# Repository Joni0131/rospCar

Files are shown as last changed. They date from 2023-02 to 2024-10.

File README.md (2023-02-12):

- [rospCar](#rospcar)
- [Work progression](#work-progression)
  - [1. Old System](#1-old-system)
  - [2. Planning](#2-planning)
  - [3. ESP-32](#3-esp-32)
  - [4. Brain](#4-brain)
- [Resume](#resume)

# rospCar

This repository contains the whole redevelopment of an old RC car.
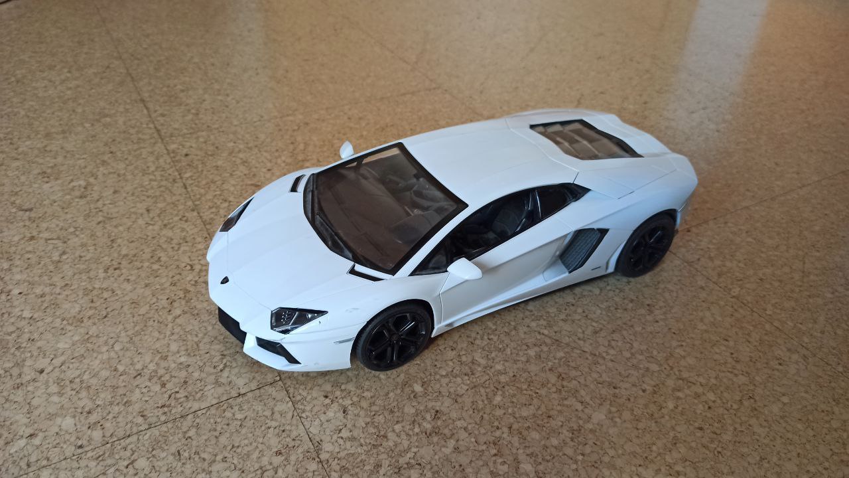
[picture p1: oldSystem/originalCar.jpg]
Old Car

To change the control system to an esp32 and a ROS communication with the computer to potentially implement a SLAM algorithm.

# Work progression

I structured my work in the following four steps. Those are shortly discussed on this page for more detailed information on each step please correspond to each designated page.

## 1. [Old System](oldSystem/)

The first step of the redevelopment process consists of understanding and checking the currently used electronics. As well as their functionality.

## 2. [Planning](upgradePlan/)

In the second phase, I chose the requirements for the new car, ordered parts that fulfill those requirements as well as designed the new circuit diagram.

## 3. [ESP-32](esp/)

The third step is considered the heart of the hardware development process. Here I define the functional requirements for the esp-32 and implement those decently.

## 4. [Brain](brain/)

Last but not least I design the other side of the communication and control algorithm for this project on the computer. The computer software is calculating the movements of the car and is using the sensor data to do this. Furthermore, it will be using a SLAM algorithm to map the whole area and it will be possible to go to certain locations easily.

# Resume

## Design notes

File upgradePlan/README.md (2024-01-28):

- [2. Planning](#2-planning)
  - [2.1 Funktional requiremnets](#21-funktional-requiremnets)
  - [2.2 Reqiered Hardware](#22-reqiered-hardware)
  - [2.3 Circuit Diagram](#23-circuit-diagram)

# 2. Planning
In this folder, I am planning the improvements for the rospCar inclusive of the new circuit diagram.

## 2.1 Funktional requiremnets

The rospCar has to fulfill multiple requirements.
 - steering
 - impulsion
 - controlling
 - voltage regulation
 - communication with another device via WIFI
 - environment tracking
 - front and back lights
 - similar appearance to the old system
 - speed information
## 2.2 Required Hardware
To fulfill those requirements multiple hardware components are necessary.
- For steering, use a [SG90 Micro Servomotor](http://www.ee.ic.ac.uk/pcheung/teaching/DE1_EE/stores/sg90_datasheet.pdf). With such a motor the steering accuracy can be improved.
- The impulsion motor is defective so a new motor has to be inserted. For this, I bought a new [motor](https://www.luedeke-elektronic.de/DC-Kleinmotor-2-5V-6V-DC-210mA-14-500U-Min-MOT2.html) of a similar size.
- As a motor controllers, I am using two L9110H.
- To regulate the voltage going to the motor I am using the voltage regulator LM317T.
- Because the car should be able to communicate with another device using WIFI, I need a WIFI module. However, I want to use ROS2 as the communication system between those devices. This is a problem because on most really small microcontrollers it is not supported. I choose [micro-ROS](https://micro.ros.org/) which is capable of running on such small chips. But support for microcontrollers to communicate with WIFI is limited so I choose the [ESP-32](https://www.espressif.com/en/products/socs/esp32) as my main microcontroller.
- For environmental tracking there are multiple options:
  - <ins>Ultrasonic sensor:</ins> This is a cheap method to detect objects and their distance. However, I am not sure how accurate this tracking is gonna be and so it is a bad option for a SLAM algorithm. But I still wanna try it I bought the HC-SR04 as an ultrasonic sensor.
  - <ins>ToF sensor:</ins> Because ToF sensors can detect distances quite accurately it is a good option for a SLAM algorithm. However, it has to be kept in mind that transparent objects could not be detected. Another disadvantage of those sensors is that it only detects objects at the same height as the sensor. Even though I decided I want to use such a sensor. So I bought the VL53L0/1XV2 and will try to use those.
  - <ins>Camera:</ins> A camera would be good to get colors of the surroundings as well as a huge part of it. Because of the lens. I am currently not sure if I will be using a camera however if I want to add one I will be adding the 0V2640 camera to the ESP-32.
- The lights of the old system can still be used.
- The speed of the rospCar is detected with an accelerometer ITG/MPU6050/GY-521.
- For the electric circuit, I need a few resistors, capacitors and wires.
## 2.3 Circuit Diagram
### 2.3.1 V0.1
To test that the baisic functionality of driving and steering is working my circuit design does not include any environment sensors only the acceleration sensor, the motors and the LED's.
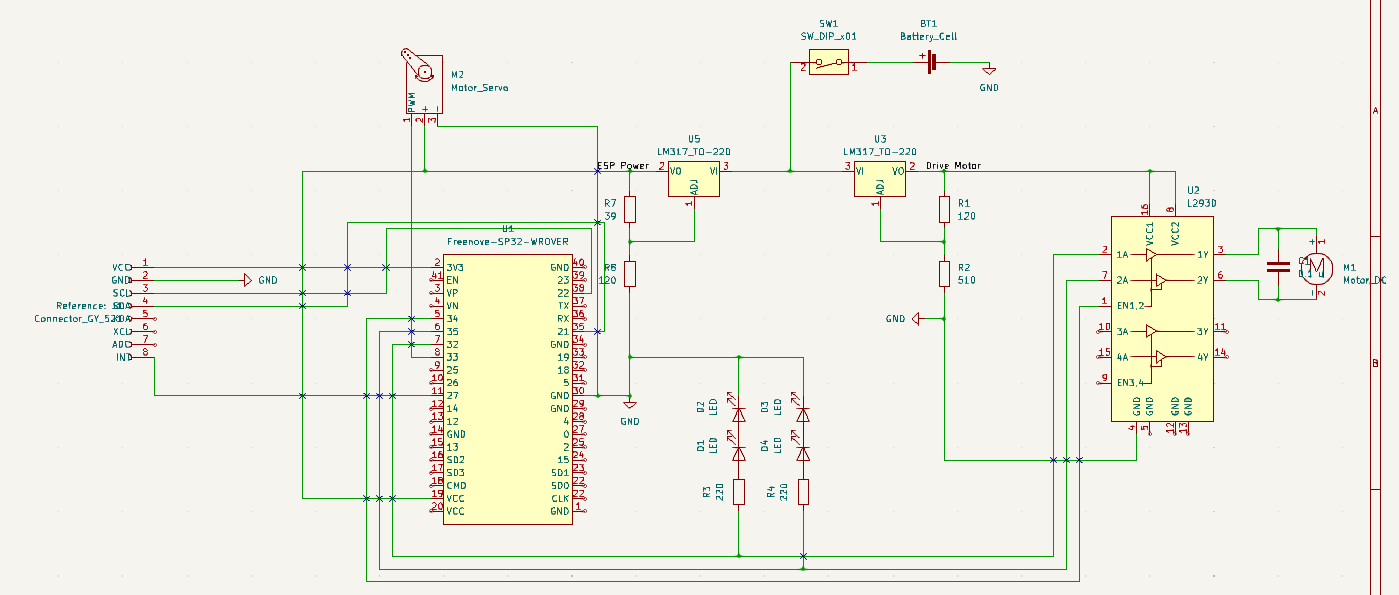
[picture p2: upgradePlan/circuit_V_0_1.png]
Circuit Diagram V0.1


#### 2.3.1.1 Learnings
When building and implementing the first functionalitis I learned that I can't use the Pin's 34-39 for output signals. Also all Pins that have the ACD2 connected can't be used because of the needed Wifi. Those the relevant pins have to be rearanged.

Also the LED's can't be connected in this way so that has to be changed as well.

For a third optimization it might be neccessary to increase the voltage for the impulsion motor drive. However, it has to be keept in mind that that voltage is also powering the L293D those it should not be overvoltaged. It can also be considered to exchange the LM317 for another trasformer that is cappable of higher current.

### 2.3.2 V0.2
To fully implement and to consider all hardware limitations I am now adding a Ultarsonic and Time-of-Flight sensor to the system including some of the learnings from before.
Circuit Diagram V0.2

#### 2.3.2.1 Learning
The motor is still not starting without help and the motor will get power in the boot process because the motor driver is enabled when it is booting.

### 2.3.3 V0.3
To get the motor starting I separated the Power circuit for the L293D and the motor power circuit. I also added a inverter based on a transistor for the enable signal for the motor driver because the esp pin will always be in the HIGH state in the boot process.
Circuit Diagram V0.3

## 2.4 PCB design

After a few schematic iterations I started designing the PCB.

### 2.4.1 V0.3
To design the PCB I added footprints to all the schematic symbols in KiCad and than placed it on a board. I then used FreeRouting to do a first automated routing for the PCB. I decided that the width of each lane is with 1 mm more than enough to handle the load of the system.

Because this is my first designed board and also the first prototype I did not optimize the length of each line and those reduced latency. In this setup it is more than enough like that and can be done in the future.

PCB Layout V0.3

Here a not complete 3D image of the planed PCB.
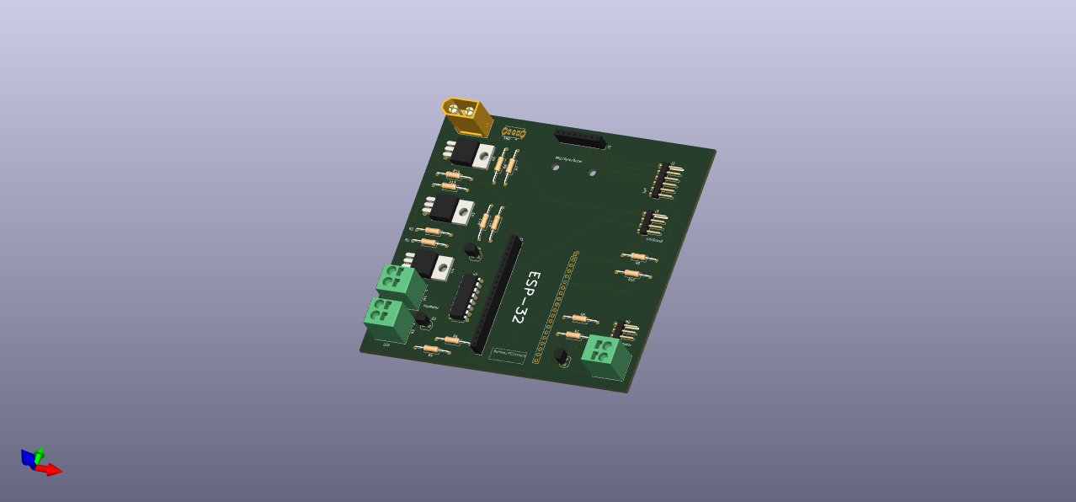
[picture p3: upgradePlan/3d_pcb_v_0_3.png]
3D PCB V0.3
 

And here the first soldered PCB.
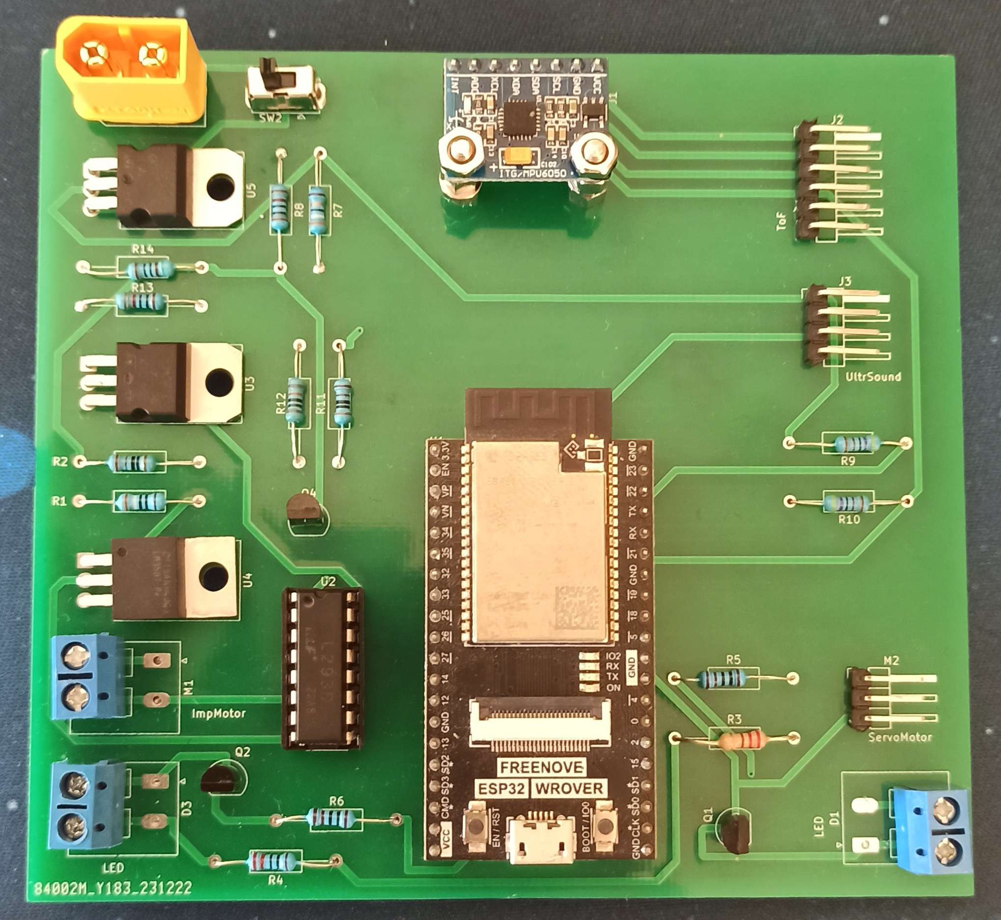
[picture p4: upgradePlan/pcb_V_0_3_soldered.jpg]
PCB V0.3 Soldered


#### 2.4.1.1 Learningdd

The pcb is still way to big. Those the next iteration needs to be smaller. Another learning is that the motor controller and the 3 voltage regulators are getting quite hot after a short test. Those I will add some kind of heat sink to them.

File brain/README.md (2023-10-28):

- [4. Brain](#4-brain)
  - [4.1 Requirements](#41-requirements)
  - [4.2 Realisation](#42-realisation)

# 4. Brain

## 4.1 Requirements

- The Brain is using ROS2 to communicate with the ESP
- The Brain sends controll instructions to the ESP
- The Brain is collecting and processing the sensor data.

Later:
- The Brain is using the sensor data to derive the controll instructions
- The Brain is using a SLAM algorithm.

## 4.2 Realisation

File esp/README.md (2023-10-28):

- [3. ESP-32](#3-esp-32)
  - [3.1 Requierements](#31-requierements)
  - [3.2 Realisation](#32-realisation)

# 3. ESP-32 

## 3.1 Requierements

- The code should be written and compiled with PlatformIO
- The ESP32 is using microROS to communicate with the Brain that is running ROS2
- The ESP has to controll the motors.
- It has to collect the sensor data and send it to the Computer.

## 3.2 Realisation

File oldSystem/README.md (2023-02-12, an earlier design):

- [1. Old System](#1-old-system)
  - [1.1 Components](#11-components)
  - [1.2 Schematic](#12-schematic)
  - [1.3 Testing](#13-testing)
    - [1.3.1 FA-130](#131-fa-130)
    - [1.3.2 260s-18130-38](#132-260s-18130-38)

# 1. Old System

I opened the car cover to reveal the internal structure of the RC car.<br>
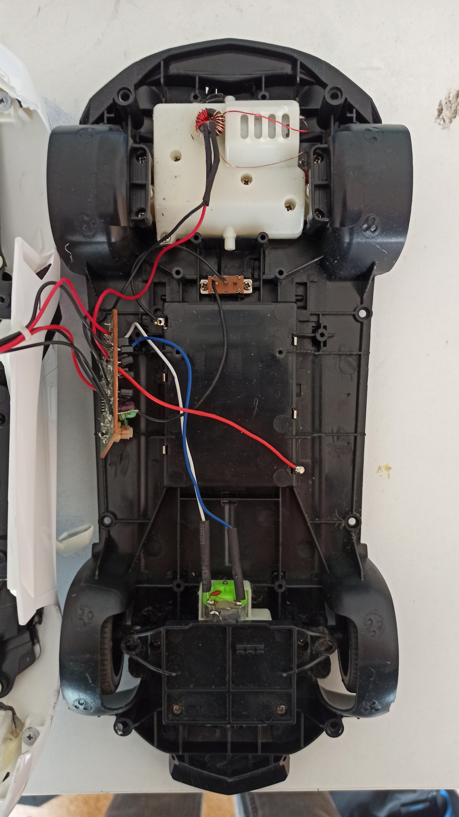
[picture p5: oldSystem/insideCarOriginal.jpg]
insideCarOriginal
<br>
As can be seen, the car's internals is pretty basic.

## 1.1 Components

- 1x FA-130 motor (steering)
- 1x 260s-18130-38 motor (impulsion)
- 1x RX-2C (controller)
- 1x PCB
- 2x C8050 (transistor)
- 2x C8550 (transistor)
- 2x D882 (transistor)
- 2x B772 (transistor)
- 4x C9014 (transistor)
- LEDs
- cable
- batterie department
- resistors 
- capacitors
- wires
- power switch

## 1.2 Schematic

To understand the control system of the RC car I partially analyzed the PCB and drama and created a [circuit diagram](initialSystem/) in kicad based on those observations.<br>
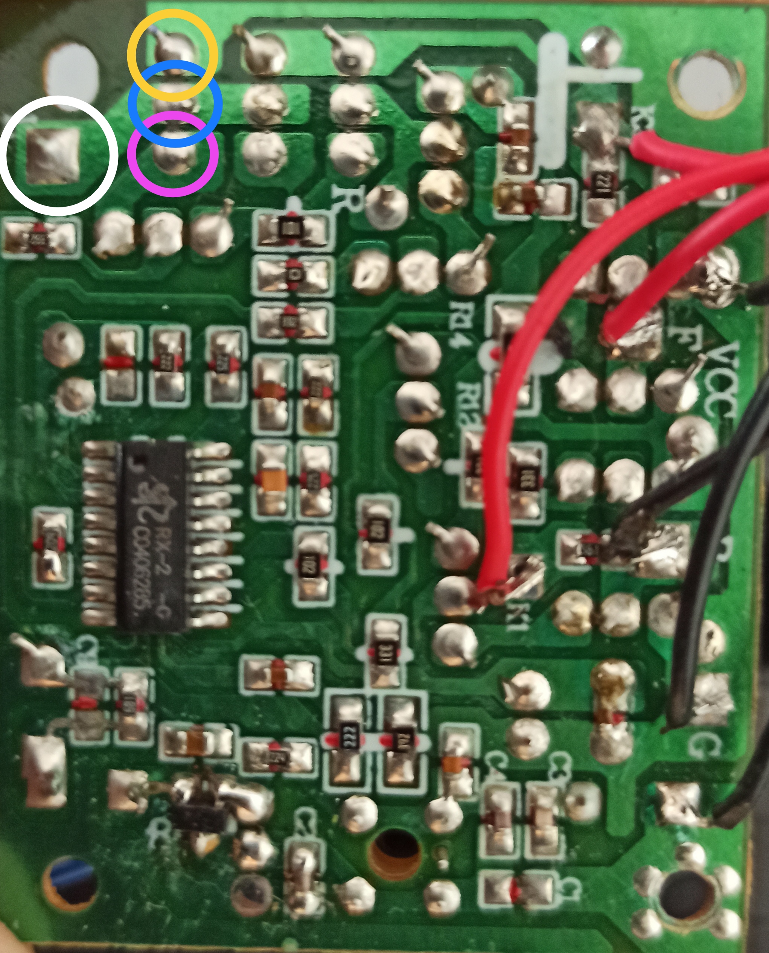
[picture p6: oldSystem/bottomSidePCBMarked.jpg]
bottomSidePCBMarked

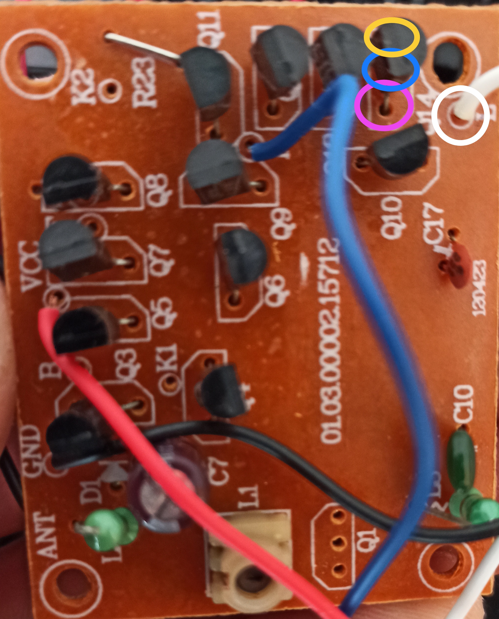
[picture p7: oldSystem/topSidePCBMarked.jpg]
topSidePCBMarked
<br>
Here is the partial circuit diagram as an image.<br>
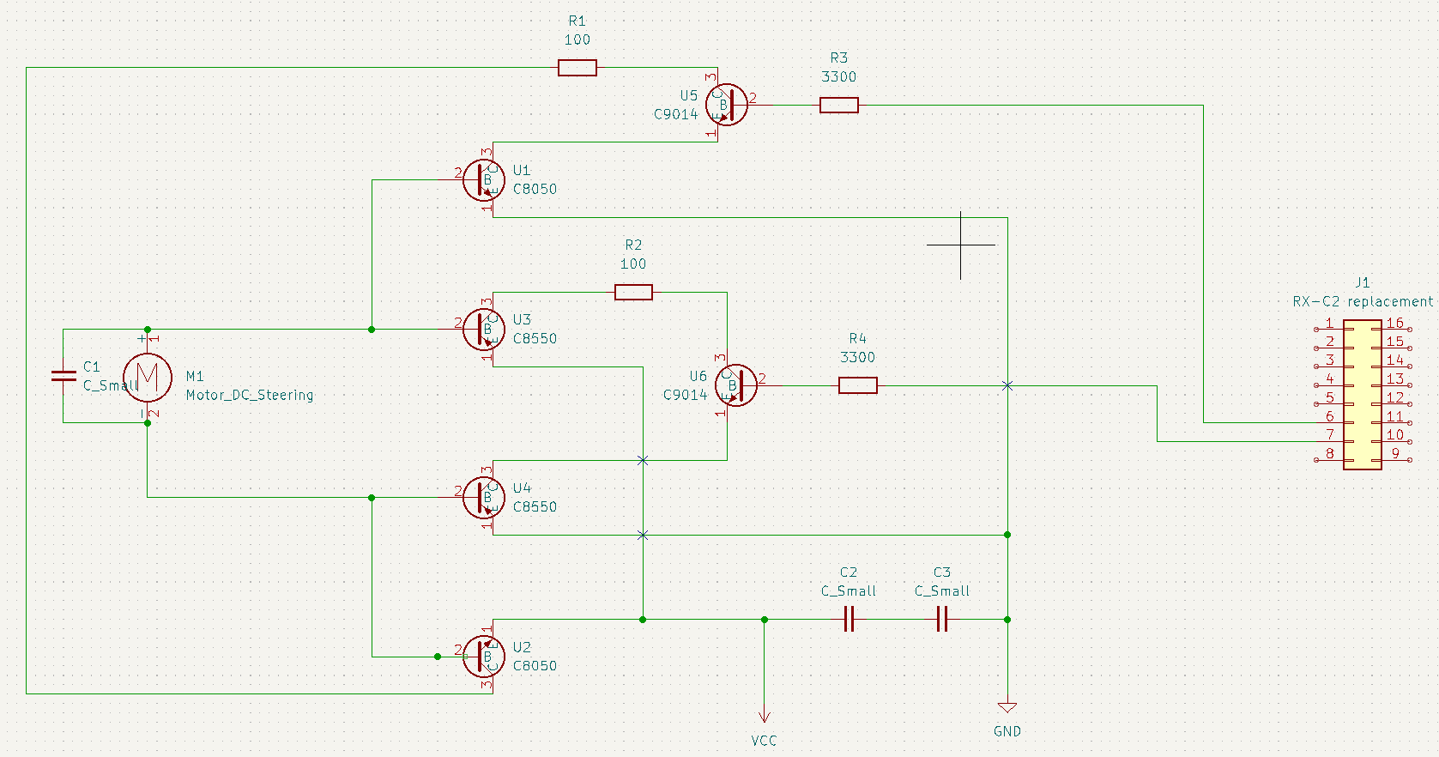
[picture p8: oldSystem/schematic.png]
schematic


However, I am a bit confused because the motor is connected to the middle part of all 4 transistors which is normally used to control the current running through the transistor. So I am not sure if I made an error creating the schematic based on the PCB or if there is some other information that I am missing.
So if anyone has an explanation for this I am more than happy to communicate with you regarding this issue.

## 1.3 Testing

Because I want to partially keep the existing system I have to test the current motors for their function.
### 1.3.1 FA-130

This [motor](https://product.mabuchi-motor.com/detail.html?id=10) is responsible for the steering of the car. I tested if the motor is still functional and this is the case so I can keep it. 
This motor has an operation Voltage of 1.5-3.0V and a maximum stall current of 2.1 Ampere.

### 1.3.2 260s-18130-38
With those engravings, I couldn't locate the exact model however it is not moving with different voltages. This means I will have to find a motor replacement that is fitting into the motor mounting place.

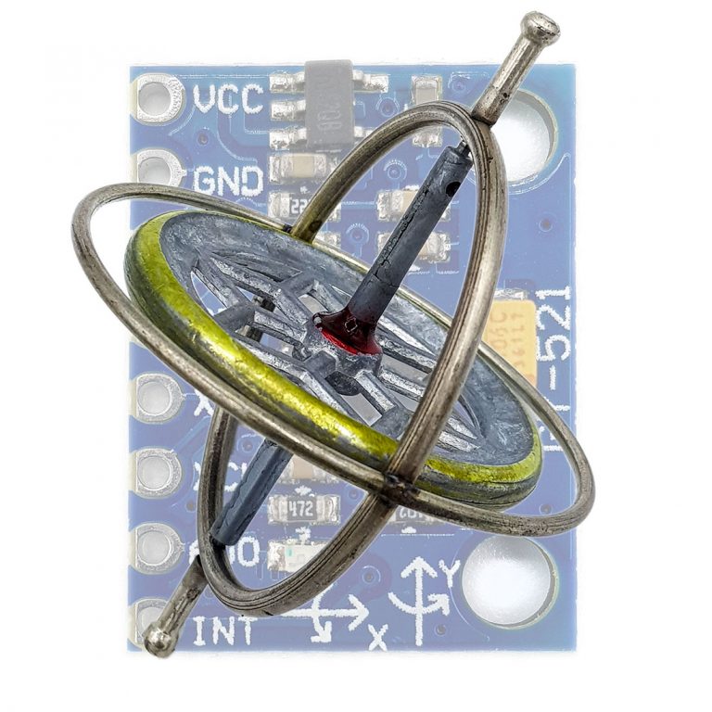
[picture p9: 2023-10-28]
upgradePlan/Datasheet/MPU6050 Beschleunigungssensor und Gyroskop • Wolles Elektronikkiste_files/Beitragsbild-768x768.jpg

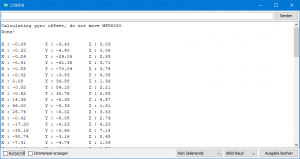
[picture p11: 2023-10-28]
upgradePlan/Datasheet/MPU6050 Beschleunigungssensor und Gyroskop • Wolles Elektronikkiste_files/mpu6050_light_get_angle-300x159.png

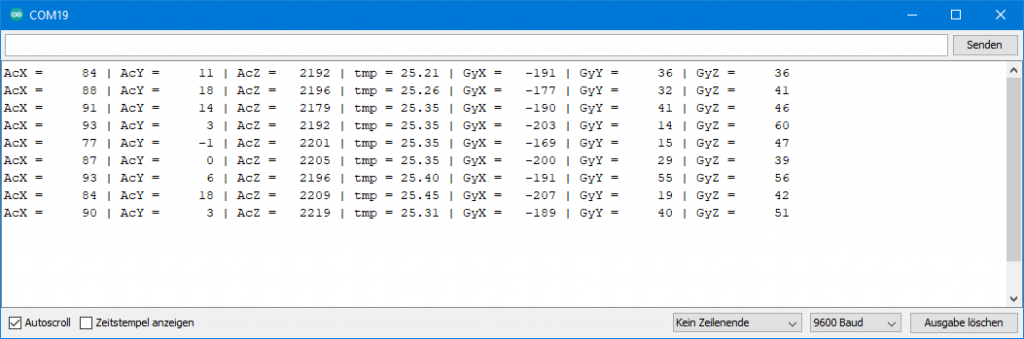
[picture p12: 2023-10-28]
upgradePlan/Datasheet/MPU6050 Beschleunigungssensor und Gyroskop • Wolles Elektronikkiste_files/Output_minimum_plus_sketch-1024x339.png

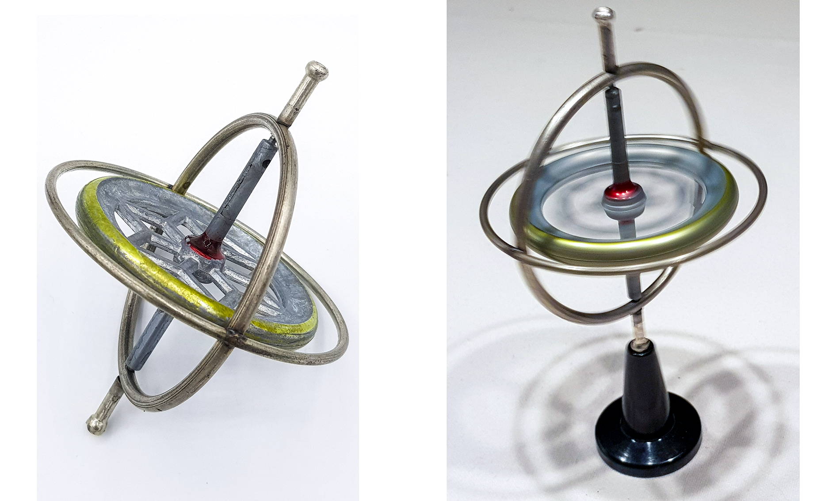
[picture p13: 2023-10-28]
upgradePlan/Datasheet/MPU6050 Beschleunigungssensor und Gyroskop • Wolles Elektronikkiste_files/Kreiselspielzeug.png

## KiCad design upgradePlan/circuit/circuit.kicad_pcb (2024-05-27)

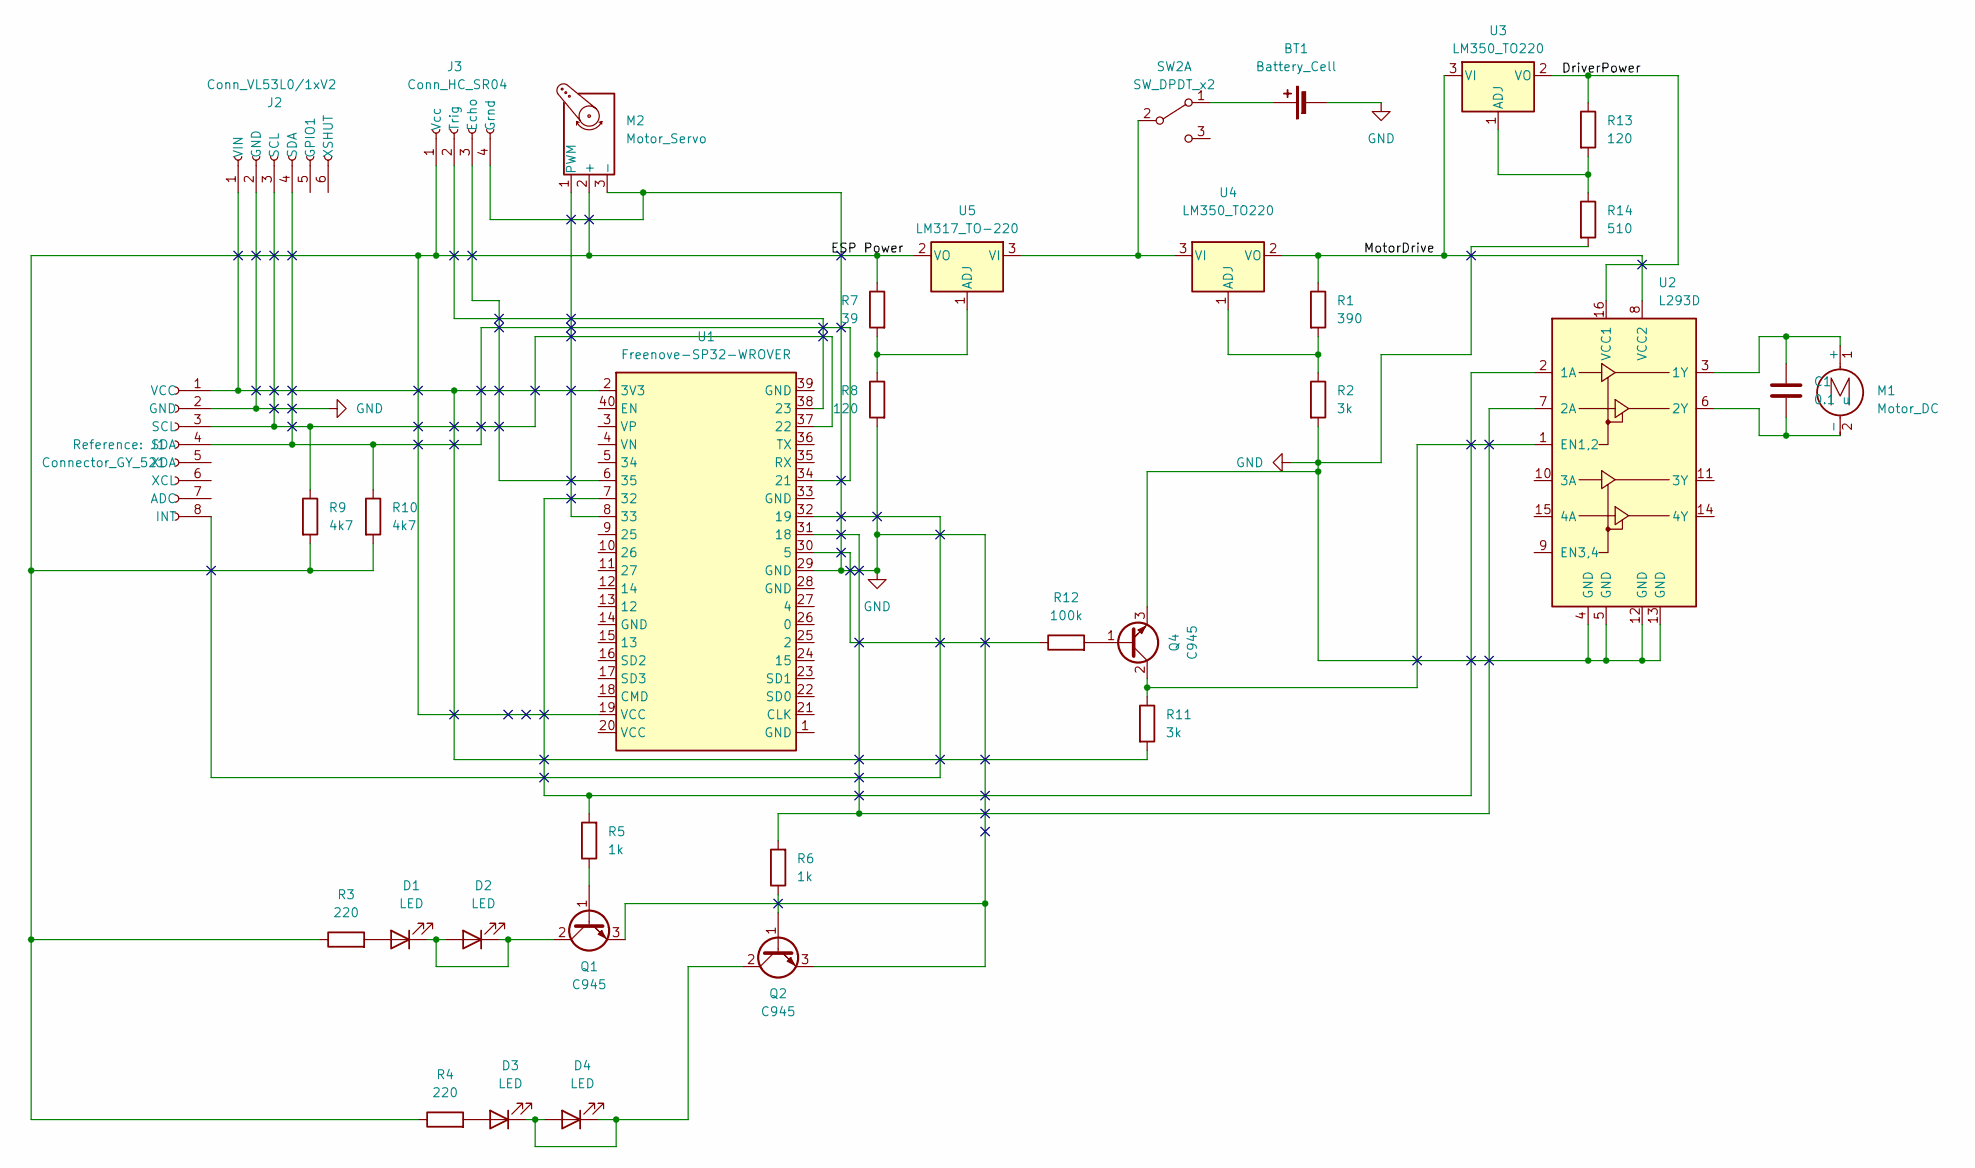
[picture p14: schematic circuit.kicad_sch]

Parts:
BT1: Battery_Cell; AMASS_XT60-M_1x02_P7.20mm_Vertical
C1: 0.1 u
D1, D3: LED; PhoenixContact_SPT_2.5_2-V-5.0-EX_1x02_P5.0mm_Vertical
D2, D4: LED
J1: Connector_GY_521; GY-521
J2: Conn_VL53L0/1xV2; PinHeader_1x06_P2.54mm_Horizontal
J3: Conn_HC_SR04; PinHeader_1x04_P2.54mm_Horizontal
M1: Motor_DC; PhoenixContact_SPT_2.5_2-V-5.0-EX_1x02_P5.0mm_Vertical
M2: Motor_Servo; PinHeader_1x03_P2.54mm_Horizontal
Q1, Q2, Q4: C945; TO-92
R1: 390; R_Axial_DIN0207_L6.3mm_D2.5mm_P15.24mm_Horizontal
R2, R11: 3k; R_Axial_DIN0207_L6.3mm_D2.5mm_P15.24mm_Horizontal
R3, R4: 220; R_Axial_DIN0207_L6.3mm_D2.5mm_P15.24mm_Horizontal
R5, R6: 1k; R_Axial_DIN0207_L6.3mm_D2.5mm_P15.24mm_Horizontal
R7: 39; R_Axial_DIN0207_L6.3mm_D2.5mm_P15.24mm_Horizontal
R8, R13: 120; R_Axial_DIN0207_L6.3mm_D2.5mm_P15.24mm_Horizontal
R9, R10: 4k7; R_Axial_DIN0207_L6.3mm_D2.5mm_P15.24mm_Horizontal
R12: 100k; R_Axial_DIN0207_L6.3mm_D2.5mm_P15.24mm_Horizontal
R14: 510; R_Axial_DIN0207_L6.3mm_D2.5mm_P15.24mm_Horizontal
SW2: SW_DPDT_x2; SW_Slide_1P2T_CK_OS102011MS2Q
U1: Freenove-SP32-WROVER; MyESPConnector
U2: L293D; DIP-16_W7.62mm
U3, U4: LM350_TO220; TO-220-3_Horizontal_TabDown
U5: LM317_TO-220; TO-220-3_Horizontal_TabDown

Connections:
/DriverPower: R13.1, U2.16 (VCC1), U3.2 (VO)
/ESP Power: J3.1 (Vcc), M2.2 (+), R3.1, R4.1, R7.1, R9.2, R10.2, U1.19 (VCC), U5.2 (VO)
/MotorDrive: R1.1, U2.8 (VCC2), U3.3 (VI), U4.2 (VO)
GND: BT1.2 (-), J1.2 (GND), J2.2 (GND), J3.4 (Grnd), M2.3 (-), Q1.3 (E), Q2.3 (E), Q4.3 (E), R2.2, R8.2, R14.2, U1.29 (GND), U2.4 (GND), U2.5 (GND), U2.12 (GND), U2.13 (GND)
unnamed: BT1.1 (+), SW2.1 (A)
unnamed: D1.2 (A), R3.2
unnamed: D1.1 (K), D2.1 (K), D2.2 (A), Q1.2 (C)
unnamed: D3.2 (A), R4.2
unnamed: D3.1 (K), D4.1 (K), D4.2 (A), Q2.2 (C)
unnamed: J1.8 (INT), U1.32 (19)
unnamed: J1.3 (SCL), J2.3 (SCL), R9.1, U1.37 (22)
unnamed: J1.4 (SDA), J2.4 (SDA), R10.1, U1.34 (21)
unnamed: J1.1 (VCC), J2.1 (VIN), R11.2, U1.2 (3V3)
unnamed: J3.3 (Echo), U1.6 (35)
unnamed: J3.2 (Trig), U1.38 (23)
unnamed: C1.1, M1.1 (+), U2.3 (1Y)
unnamed: C1.2, M1.2 (-), U2.6 (2Y)
unnamed: M2.1 (PWM), U1.8 (33)
unnamed: Q1.1 (B), R5.1
unnamed: Q2.1 (B), R6.1
unnamed: Q4.1 (B), R12.2
unnamed: Q4.2 (C), R11.1, U2.1 (EN1,2)
unnamed: SW2.2 (B), U4.3 (VI), U5.3 (VI)
unnamed: R12.1, U1.30 (5)
unnamed: R6.2, U1.31 (18), U2.7 (2A)
unnamed: R5.2, U1.7 (32), U2.2 (1A)
unnamed: R13.2, R14.1, U3.1 (ADJ)
unnamed: R1.2, R2.1, U4.1 (ADJ)
unnamed: R7.2, R8.1, U5.1 (ADJ)

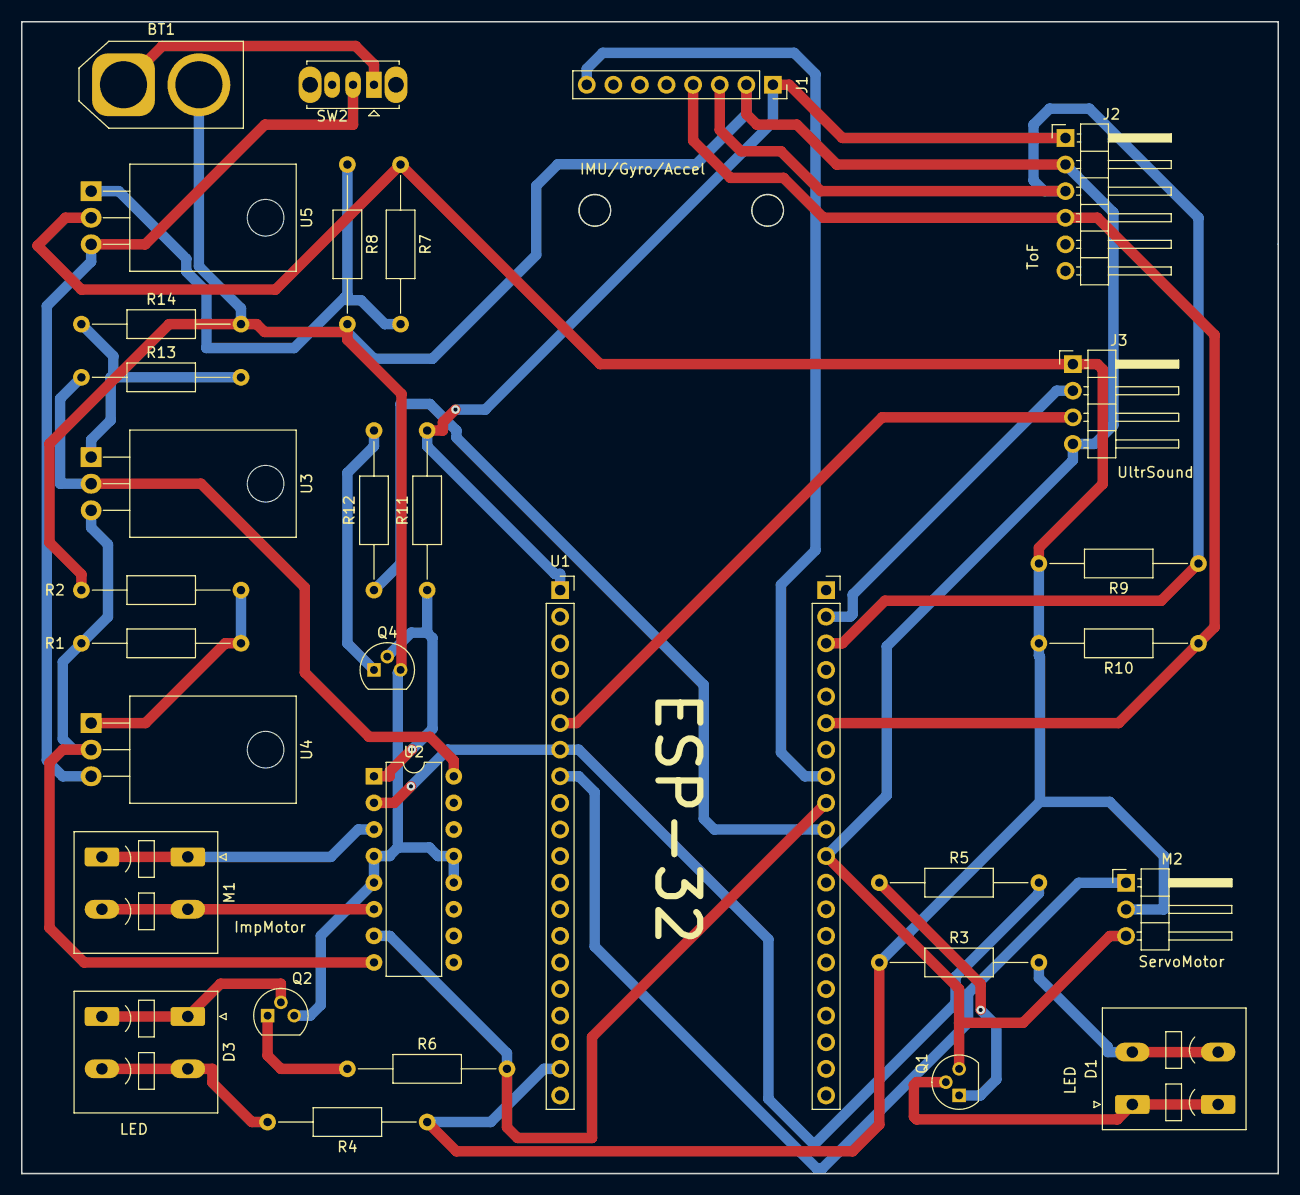
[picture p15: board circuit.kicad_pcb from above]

Board: 2 copper layers, 120.0 x 110.0 mm, 31 parts (0 on the bottom side), 29 nets.

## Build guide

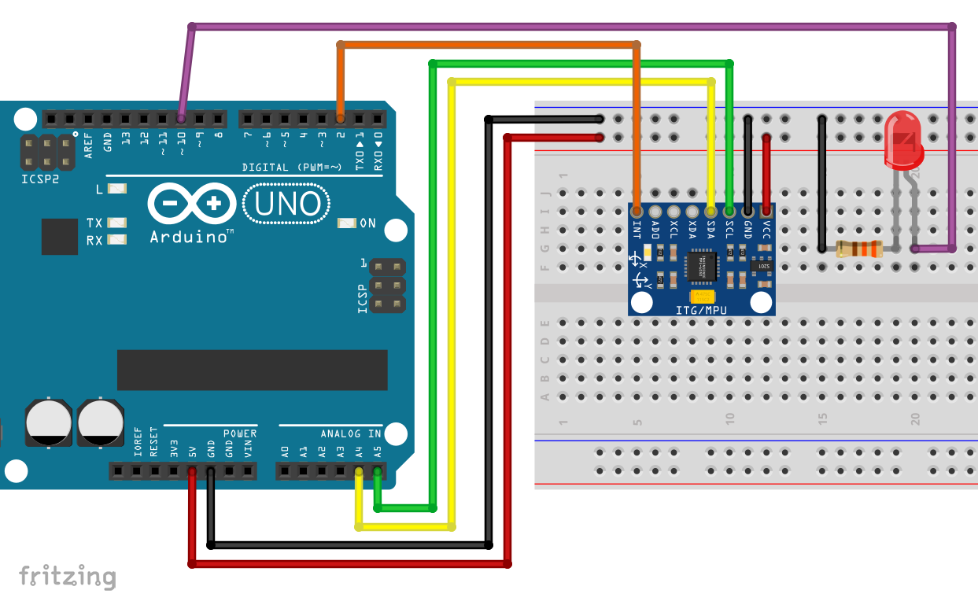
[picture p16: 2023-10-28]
upgradePlan/Datasheet/MPU6050 Beschleunigungssensor und Gyroskop • Wolles Elektronikkiste_files/MPU6050_Wiring.png

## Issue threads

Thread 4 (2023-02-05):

ESP32 software

Joni0131, 2023-02-05:
Create the software needed for ROS2 communication with the help of microRos and all sensor and motor controls.

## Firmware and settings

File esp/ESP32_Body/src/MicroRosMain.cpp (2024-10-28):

#include "MicroRosMain.h"

rcl_allocator_t allocator;
rclc_support_t support;
rcl_node_t node;

void error_loop()
{
    while (1)
    {
        delay(100);
    }
}

void initMicroRos()
{
    Serial.println("Start Wifi.");
    setupWifi();
    Serial.println("Start Alloctor.");
    setupAllocator();
    Serial.println("Start Init Options.");
    createInitOptions();
    Serial.println("Start Node.");
    createNode();
}

void createNode()
{
    // create node
    RCCHECK(rclc_node_init_default(&node, "micro_ros_platformio_node", "", &support));
}

void createInitOptions()
{
    // create init_options
    RCCHECK(rclc_support_init(&support, 0, NULL, &allocator));
}

void setupWifi()
{
    IPAddress ipAddress = IPAddress(IPADDRESS); // IP Address of recieving device
    String ssid = SSID;
    String pass = PASSWORD;

    set_microros_wifi_transports(ssid.begin(), pass.begin(), ipAddress, 8888);
    delay(2000);
}

void setupAllocator()
{
    allocator = rcl_get_default_allocator();
}

void setupService()
{
    const rosidl_service_type_support_t * my_service_type_support = ROSIDL_GET_SRV_TYPE_SUPPORT(std_srvs, srv, Empty);
    // create service
    RCCHECK(rclc_service_init(&service, &node, ROSIDL_GET_SRV_TYPE_SUPPORT(std_srvs, srv, Empty), "add_two_ints"));
}

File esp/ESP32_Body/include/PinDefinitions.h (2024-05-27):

#ifndef PINDEFINITIONS_H
#define PINDEFINITIONS_H

#define PIN_ACCELEROMETER_INTERUPT 19

#define PIN_STEERING_MOTOR 33

#define PWM_CHANNEL0 0
#define PWM_CHANNEL1 1
#define PWM_CHANNEL2 2
#define PWM_CHANNEL3 3
#define PWM_CHANNEL4 4
#define PWM_FREQ 5000
#define PWM_RESO 8

#define PIN_IMPULSION_FORWARD 18
#define PIN_IMPULSION_BACKWARD 32
#define PIN_IMPULSION_ENABLE 5
#define PWM_CHANNEL_FORWARD 5
#define PWM_CHANNEL_BACKWARD 6

#define PIN_ULTRASOUND_TRIG 23
#define PIN_ULTRASOUND_ECHO 35

#endif

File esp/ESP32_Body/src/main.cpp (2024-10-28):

#include "main.h"

// #if !defined(MICRO_ROS_TRANSPORT_ARDUINO_SERIAL)
// #error This example is only avaliable for Arduino framework with serial transport.
// #endif

void setup()
{
  Serial.begin(115200);

  Serial.println("Start Setup.");

  setupAll();

  generatePublishers();
  addAllToExecutor();

  generateSubscribers();

  Serial.println("finished setup");
}

void loop()
{
  spinPub();
  spinSub();
  spinSrv();
  //Serial.println(digitalRead(18));
}

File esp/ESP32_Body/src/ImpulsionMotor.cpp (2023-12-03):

#include "ImpulsionMotor.h"

ImpulsionTopicInfo m_oImpulsionTopicInfo;
ImpulsionTopicTarget m_oImpulsionTopicTarget;


void setupImpulsionMotor()
{
    Serial.println(F("Initializing Impulsion motor..."));

    m_oImpulsionTopicInfo.msg_type = *ROSIDL_GET_MSG_TYPE_SUPPORT(custom_interfaces, msg, ImpulsionMotor);
    m_oImpulsionTopicTarget.msg_type = *ROSIDL_GET_MSG_TYPE_SUPPORT(custom_interfaces, msg, ImpulsionMotor);
    m_oImpulsionTopicInfo.msg.id = 0;
    m_oImpulsionTopicTarget.msg.id = 0;

    pinMode(PIN_IMPULSION_ENABLE, OUTPUT);
    ledcAttachPin(PIN_IMPULSION_FORWARD, PWM_CHANNEL_FORWARD);
    ledcAttachPin(PIN_IMPULSION_BACKWARD, PWM_CHANNEL_BACKWARD);
    ledcWrite(PIN_IMPULSION_FORWARD, 0);
    ledcWrite(PIN_IMPULSION_BACKWARD, 0);
    digitalWrite(PIN_IMPULSION_ENABLE, LOW);

    Serial.println(F("Impulsion motor ready."));
}

void impulsion_timer_callback(rcl_timer_t *timer, int64_t last_call_time)
{
    RCLC_UNUSED(last_call_time);
    if (timer != NULL)
    {
        int forward = ledcRead(PWM_CHANNEL_FORWARD);
        int backward = ledcRead(PWM_CHANNEL_BACKWARD);
        int dir = 0;
        int pwm = 0;
        if (forward > 0)
        {
            dir = 1;
            pwm = forward;
        }
        else if (backward > 0)
        {
            dir = -1;
            pwm = backward;
        }
        m_oImpulsionTopicInfo.msg.direction = dir;
        m_oImpulsionTopicInfo.msg.pwm = pwm;
        RCSOFTCHECK(rcl_publish(&(publishers[m_oImpulsionTopicInfo.publisherID]), &m_oImpulsionTopicInfo.msg, NULL));
    }
}

void impulsion_subscriber_callback(const void *msgin)
{
    // Cast received message to used type
    const custom_interfaces__msg__ImpulsionMotor *local_msg = (const custom_interfaces__msg__ImpulsionMotor *)msgin;
    if (local_msg->direction == 1)
    {
        if (local_msg->pwm > MAXIMPULSIONSPEED)
        {
            ledcWrite(PWM_CHANNEL_BACKWARD, 0);
            ledcWrite(PWM_CHANNEL_FORWARD, MAXIMPULSIONSPEED);
            m_oImpulsionTopicTarget.msg.pwm = MAXIMPULSIONSPEED;
        }
        else if (local_msg->pwm > 0)
        {
            ledcWrite(PWM_CHANNEL_BACKWARD, 0);
            ledcWrite(PWM_CHANNEL_FORWARD, local_msg->pwm);
            m_oImpulsionTopicTarget.msg.pwm = local_msg->pwm;
        }
        else
        {
            ledcWrite(PWM_CHANNEL_BACKWARD, 0);
            ledcWrite(PWM_CHANNEL_FORWARD, 0);
            m_oImpulsionTopicTarget.msg.pwm = 0;
        }
    }
    else if (local_msg->direction == -1)
    {
        if (local_msg->pwm > MAXIMPULSIONSPEED)
        {
            ledcWrite(PWM_CHANNEL_FORWARD, 0);
            ledcWrite(PWM_CHANNEL_BACKWARD, MAXIMPULSIONSPEED);
            m_oImpulsionTopicTarget.msg.pwm = MAXIMPULSIONSPEED;
        }
        else if (local_msg->pwm > 0)
        {
            ledcWrite(PWM_CHANNEL_FORWARD, 0);
            ledcWrite(PWM_CHANNEL_BACKWARD, local_msg->pwm);
            m_oImpulsionTopicTarget.msg.pwm = local_msg->pwm;
        }
        else
        {

            ledcWrite(PWM_CHANNEL_FORWARD, 0);
            ledcWrite(PWM_CHANNEL_BACKWARD, 0);
            m_oImpulsionTopicTarget.msg.pwm = 0;
        }
    }
    else
    {
        ledcWrite(PWM_CHANNEL_FORWARD, 0);
        ledcWrite(PWM_CHANNEL_BACKWARD, 0);
        m_oImpulsionTopicTarget.msg.pwm = 0;
    }
    m_oImpulsionTopicTarget.msg.direction = local_msg->direction;
}

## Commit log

2023-02-07 working on old circuit diagram
    [initialSystem.kicad_pcb, initialSystem.kicad_sch]
2023-02-07 Add pictures of current electronics
    Here the pictures of the front and back of the pcb as well as the whole system
2023-02-10 working on Documentation setup and circuit diagram
    [initialSystem.kicad_sch]
2023-02-12 write old system read me and documentation
    [initialSystem.kicad_sch]
2023-02-13 update plan readme, fix gitignore to ignore the backups of the kicad project
2023-02-13 Working on the circuit design
    [newCircuit.kicad_sch]
2023-02-14 motor ciurcuit in kicad partial in picture
    [newCircuit.kicad_sch, untitled.kicad_sch]
2023-07-12 Update README.md
    Updated motor driver.
2023-10-28 circuit V0.1
    [newCircuit.kicad_pcb, newCircuit.kicad_sch, untitled.kicad_sch]
2023-10-31 Changed name of the KiCadProject
    [circuit_V0_1.kicad_pcb, circuit_V0_1.kicad_sch]
2023-11-01 Changed the circuit and added struct for custom messages
    [circuit_V0_1.kicad_sch]
2023-11-02 Added new Messages for all the currently planned modules
2023-11-02 created the publisher for the accelerometer created the setup for the mpu6050
    [circuit_V0_1.kicad_sch]
2023-11-03 remoddeled the message for the accelerometer the accelerometer is now publishing it's results
2023-11-03 Added the steering servo tuning of max parameter and init based on current value missing
    [MicroRosRX.cpp, MicroRosTX.cpp, NerveSystem.cpp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]
2023-11-05 made sure steering motor is not breaking / going in a not allowed angle added first guess of motor movement range
2023-11-05 increased steering range aded impulsion motor in a working setup added the kicad autosave to the gitignore
2023-11-05 Added the HC_SR04 and the tof sensor to the schematic added the recommended changes Update the read me add datasheet for hc-sr04
    [circuit.kicad_pcb, circuit.kicad_sch]
2023-11-05 added the skeleton for the ultrasound and tof sensor MISSING Functionality
    [NerveSystem.cpp, PinDefinitions.h]
2023-11-08 Added resistor to I2C bus added setup and reading for ultrasound and tof sensor increased the max number of pub ERROR in Timer creation of the UltraSoundSensor when all others are initilized
    [circuit.kicad_sch]
2023-11-10 increased sensing distance of the ultra sound sensor if readings are off the voltage is to low
2023-11-15 Fixed the issue with a5th publoisher by combining all env sensor data in one topic
    [MicroRosTX.cpp, NerveSystem.cpp, PinDefinitions.h]
2023-11-15 fixed the loop speed so the pub and sub are working also added calibration skelleton for the accelerometer
    [Accelerometer.h, NerveSystem.cpp, main.cpp]
2023-11-17 added new inti parameters to the accelerometer and commented the default precision of the senso
2023-12-03 increased voltage for the motor added a signal inverter for the enable pin. Added that into the code as well
    [circuit.kicad_sch]
2023-12-05 added footprints to schematic and board edge
    [circuit.kicad_pcb, circuit.kicad_sch]
2023-12-06 added layout of footprints
    [circuit.kicad_pcb]
2023-12-06 added front routing with auto completed back
    [circuit.dsn, circuit.kicad_pcb, circuit.kicad_sch]
2023-12-07 Finished pcb Updated readme Generated Gerber files
    [circuit-B_Cu.gbr, circuit-B_Mask.gbr, circuit-B_Paste.gbr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]
2024-01-28 newest version of the printed pcb including updated read me for the planning
    [circuit-B_Adhesive.gbr, circuit-B_Courtyard.gbr, circuit-B_Cu.gbr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]
2024-05-27 FIxed wrong copnnection in pcb and updated code correspondingly. Switch pin 31 and 30.
    [circuit.kicad_pcb, circuit.kicad_sch]
2024-10-28 [WIP] Adding service to call the configuration of the accelerometer
